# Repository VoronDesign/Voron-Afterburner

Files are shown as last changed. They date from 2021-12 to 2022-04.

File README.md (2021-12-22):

# Voron Afterburner Upgrade

Image of Voron Afterburner

## VORON Afterburner Upgrade

Voron Logo

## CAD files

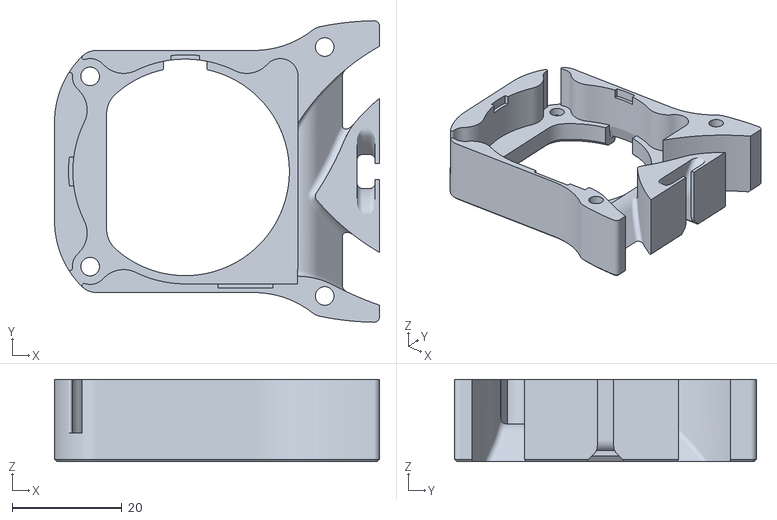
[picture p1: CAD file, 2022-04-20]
STLs/blower_housing_rear.stl
59.3 x 55.0 x 15.0

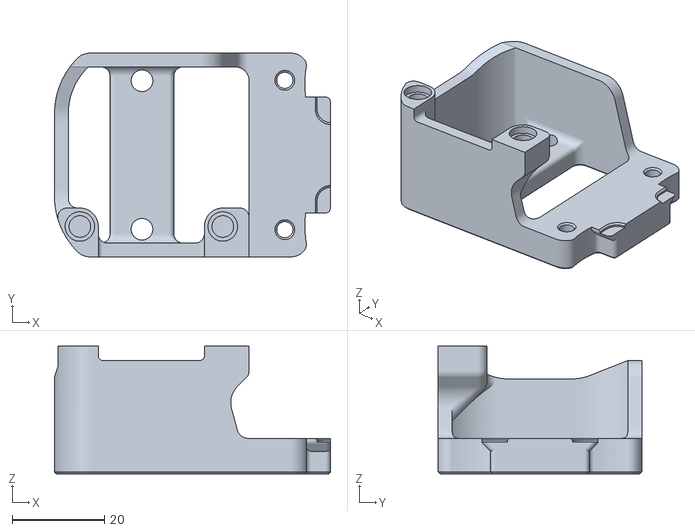
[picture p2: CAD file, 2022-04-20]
STLs/Bowden/bowden_rear.stl
59.9 x 44.2 x 27.7

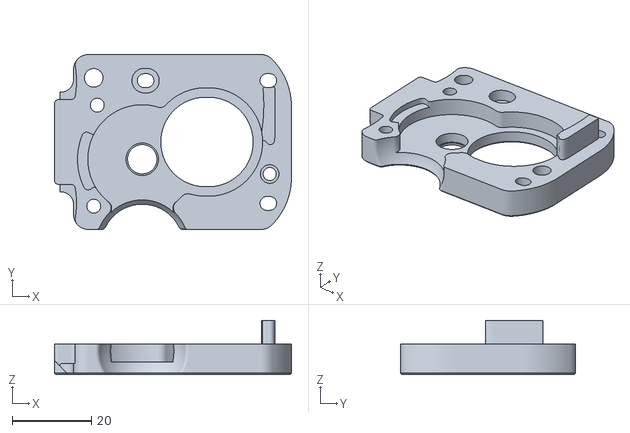
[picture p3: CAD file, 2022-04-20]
STLs/Direct_Feed/extruder_motor_plate.stl
59.9 x 44.2 x 13.7

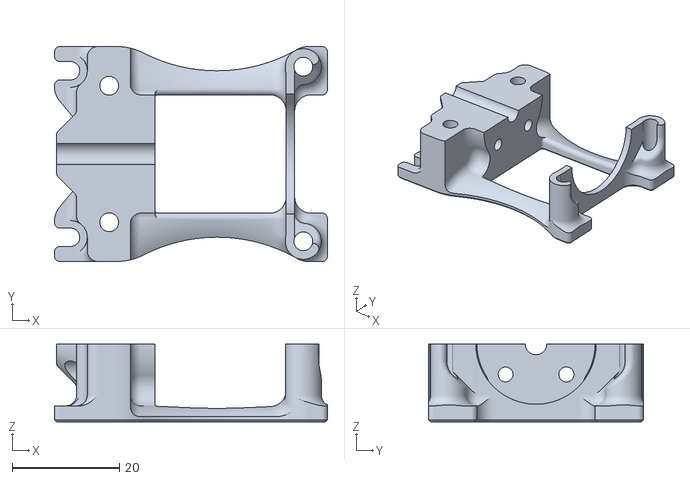
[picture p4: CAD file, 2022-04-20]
STLs/Printheads/Dragon/printhead_rear_dragon.stl
50.8 x 40.0 x 14.5

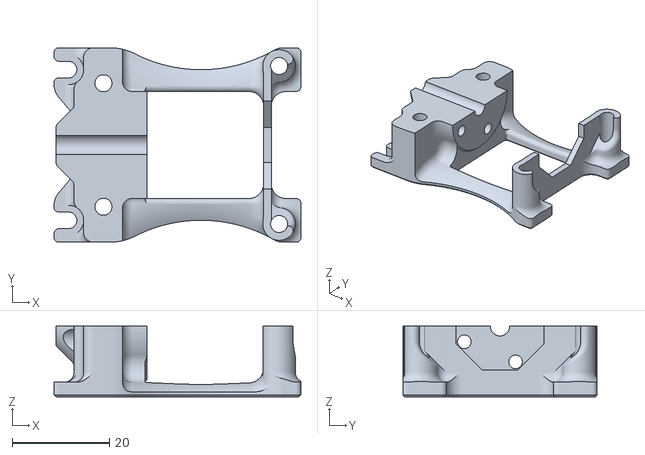
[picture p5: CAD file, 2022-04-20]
STLs/Printheads/Dragonfly_BMO/printhead_rear_dragonfly_bmo.stl
50.8 x 40.0 x 14.5

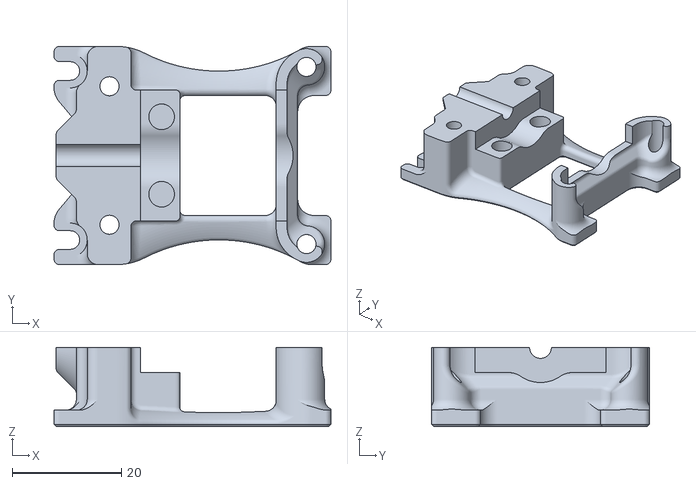
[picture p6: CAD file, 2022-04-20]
STLs/Printheads/Dragonfly_BMS/printhead_rear_dragonfly_bms.stl
50.8 x 40.0 x 14.5

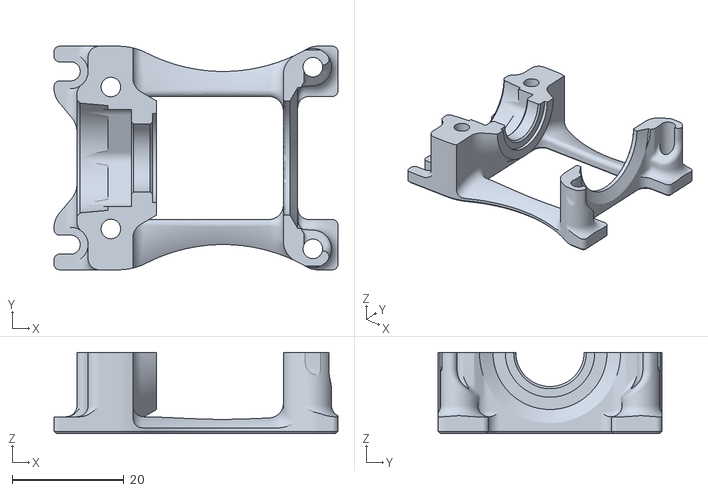
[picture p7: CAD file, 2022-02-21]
STLs/Printheads/E3D_Revo_Micro/printhead_rear_e3d_revo_micro.stl
50.8 x 40.0 x 14.5

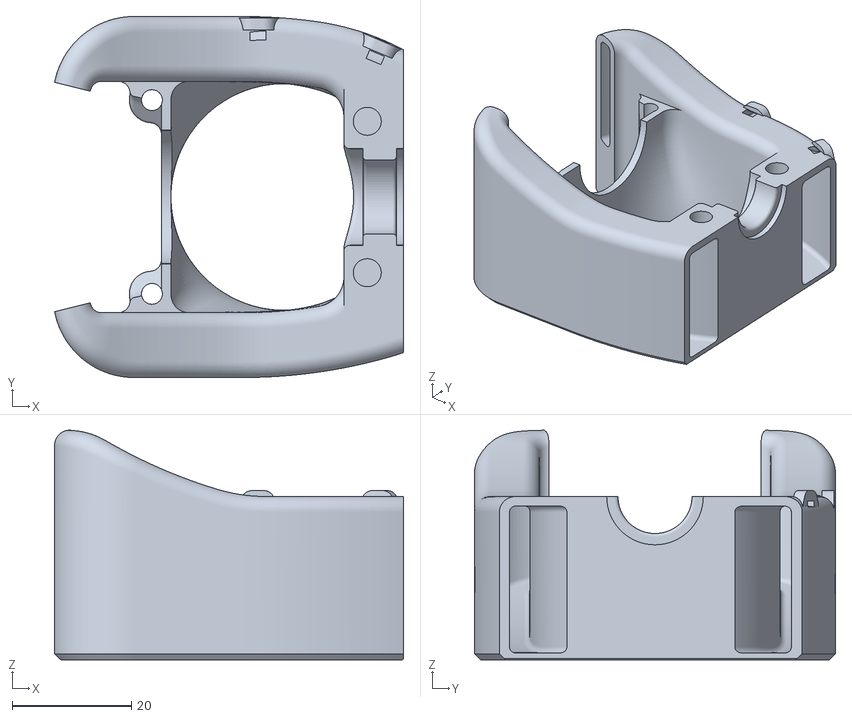
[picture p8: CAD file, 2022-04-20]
STLs/Printheads/E3D_V6/printhead_front_e3dv6.stl
58.6 x 60.6 x 38.5

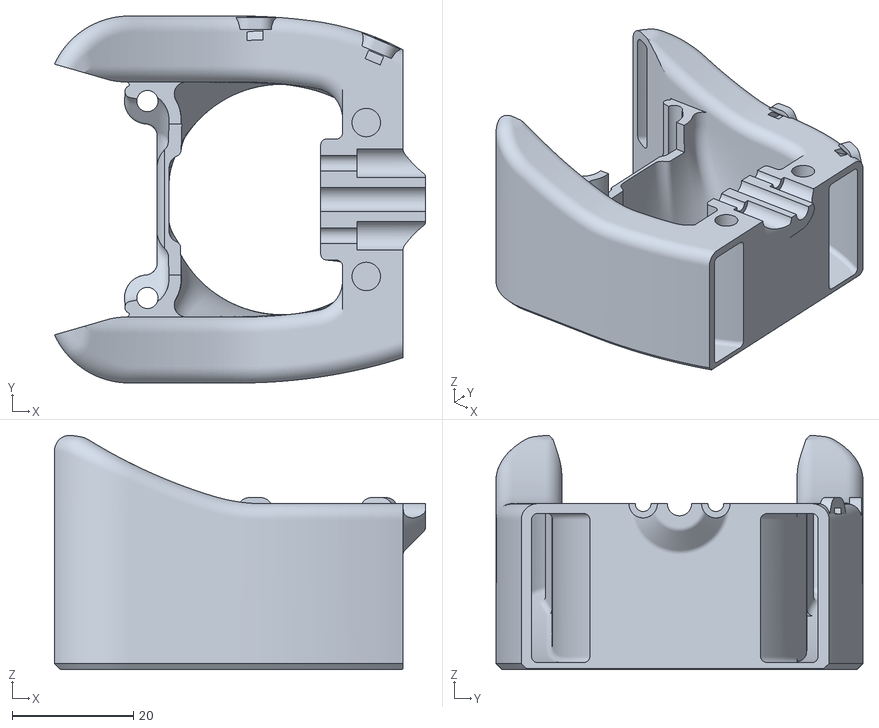
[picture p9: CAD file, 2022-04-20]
STLs/Printheads/Slice_Mosquito/printhead_front_mosquito.stl
61.2 x 60.6 x 38.7

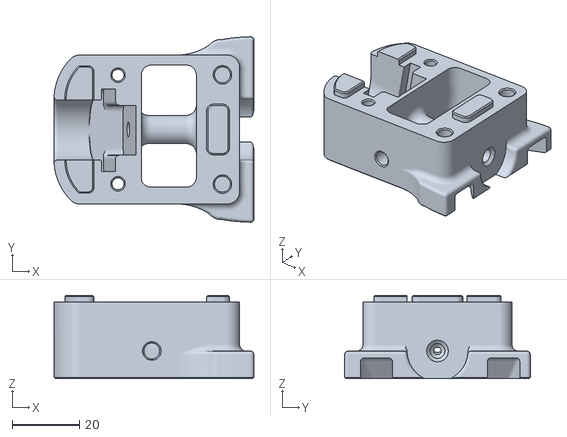
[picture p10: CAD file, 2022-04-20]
STLs/Bowden/bowden_single_front.stl
59.3 x 55.0 x 24.7

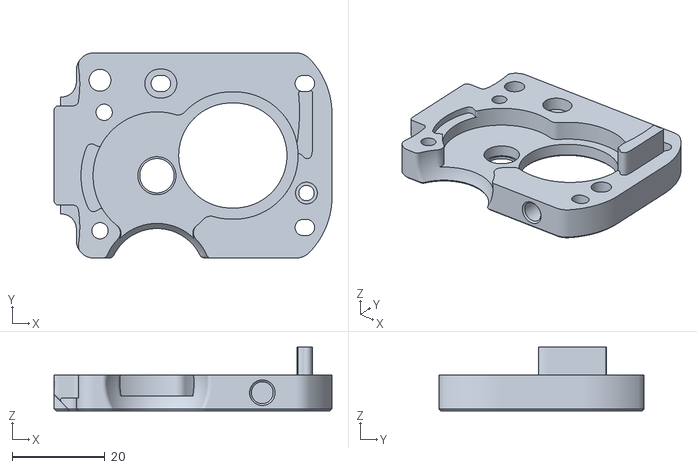
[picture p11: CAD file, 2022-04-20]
STLs/Direct_Feed/extruder_motor_plate_for_pcb.stl
59.9 x 44.2 x 13.7

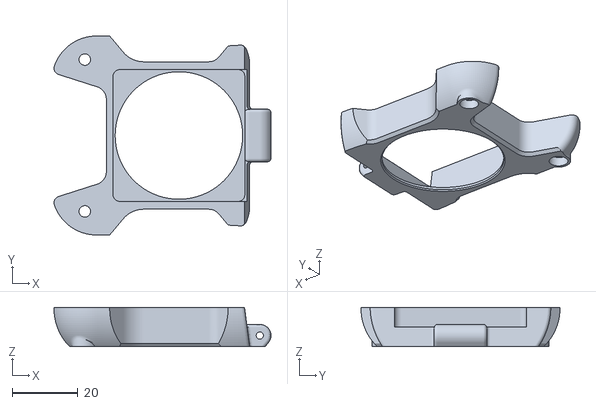
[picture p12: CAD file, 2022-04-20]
STLs/hotend_fan_mount.stl
66.1 x 60.6 x 12.0

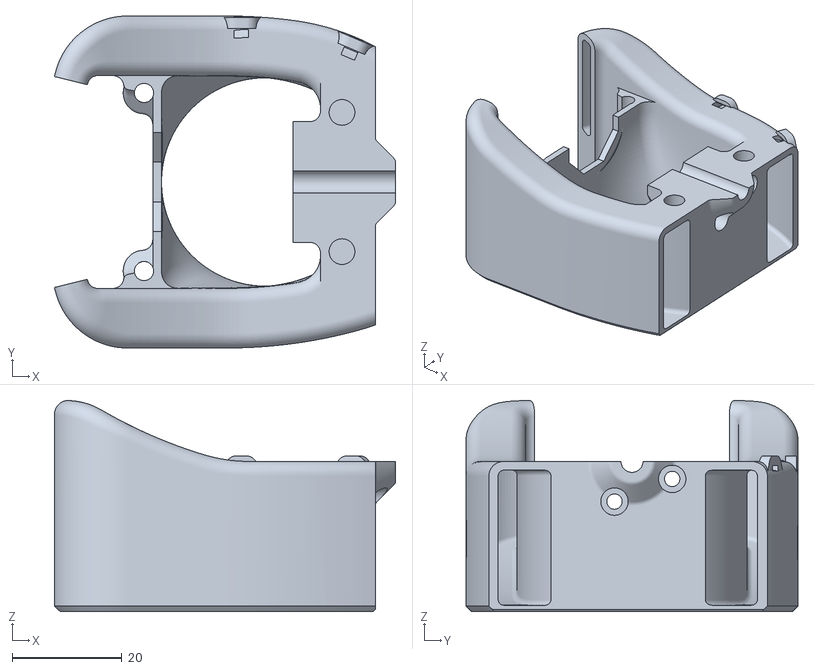
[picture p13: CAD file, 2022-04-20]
STLs/Printheads/Dragonfly_BMO/printhead_front_dragonfly_bmo.stl
62.3 x 60.6 x 38.5

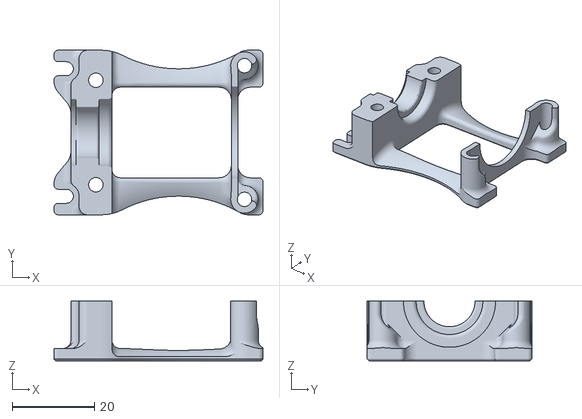
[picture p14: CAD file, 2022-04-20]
STLs/Printheads/E3D_V6/printhead_rear_e3dv6.stl
50.8 x 40.0 x 14.5

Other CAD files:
STLs/Printheads/E3D_Revo_Voron/printhead_rear_revovoron.stl
STLs/Printheads/Slice_Mosquito/printhead_rear_mosquito.stl
STLs/[a]_blower_housing_front.stl
STLs/Bowden/bowden_dual_front_a.stl
STLs/Bowden/bowden_dual_front_b.stl
STLs/Bowden/bowden_single_tl_collet_adapter.stl
STLs/Direct_Feed/[a]_connector_cover.stl
STLs/Direct_Feed/[a]_connector_cover_18.stl
STLs/Direct_Feed/[a]_guidler.stl
STLs/Direct_Feed/[a]_latch.stl
STLs/Direct_Feed/[a]_latch_shuttle.stl
STLs/Direct_Feed/chain_anchor_2hole.stl
STLs/Direct_Feed/chain_anchor_3hole.stl
STLs/Direct_Feed/chain_anchor_SW_2hole.stl
STLs/Direct_Feed/chain_anchor_SW_3hole.stl
STLs/Direct_Feed/extruder_body.stl

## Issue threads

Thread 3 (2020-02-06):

More room for 30 mm rods in XX joints

Kruppes, 2020-02-06:
With a 30,0 mm rod being perfectly flush with the bottom bearing it sticks out of the top bearing ~1mm. This makes the rod touch the printed part and block the rotation once fully assembled. Since the pulley is glued into place it can not be corrected easily after assembly and finding out.

 Can you reduce a little more material above to give room for non perfect alignment or add the ideal position of the pulley (in mm length of the rod sticking out on each side).

FHeilmann, 2020-10-15:
Since Afterburner has since left the beta stage (I assume this issue pertains to the beta release) I'm going to close this issue, if the issue is still present on the release version, feel free to reopen it!

-Florian

Closed 2020-10-15.

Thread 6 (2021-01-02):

Inconsistent extrusion / Z Banding

Roycinger, 2021-01-02:
Hi,
first and foremost I would like to bring this issue to attention where we can track it all together properly. Discord doesn't seem the right place for me as messages and focused discussions get overscrolled and interrupted with non-related topics very quickly.
Before I start I want to mention that I don't expect this issue to get solved by the Voron Team alone. Moreover, I want to evaluate this together with you so that the entire Voron community can benefit from it.

I started facing this extrusion issue when I completed my 100%-built-by-specc Switchwire. In the beginning I was thinking that the printer wasn't properly tuned yet. So I went through all the tuning steps (aligning belts, rails, tuning for filament, E-steps, run_current etc). The result didn't improve within about 90 or more test prints (where I tested every single extrusion related slicer and firmware setting).
Over the course of a few weeks, I partly reassembled the SW again, paying special attention for accuracy, squareness, etc, results didn't improve. At this point I was still under the impression that the issue was on my side as the issue still persists.
To rule out the AB, I converted my SW to bowden and the issue was gone! So I came to the conclusion that there might be a problem with the AB itself.
Because of that, I reprinted the Clockwork parts, changed the TL gears, changed all bearings, changed the motor, changed the entire hotend, precisely cut the PTFE tube. No change in results at all.
For informational purposes, this is my config: https://pastebin.com/nyULd4ca
Fast forward:
Up to yesterday, I noticed that more and more people are facing the same or similar issues, even if they might be fine with the results.
I got sent a plethora of pictures which I was allowed to use in this Git issue. They all more or less show the same problem,
Please note that most pictures where shot with "bad" light, directly from the top to make the issue apparent.
These are kinda mixed from specc-built v2.4's and SW's.
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
Cubes from my SW:
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
Random v0 part printed with my SW:
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
Another set of v0 parts:
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

For my part, I could rule out any looseness in the kinematics or topics related to filament (as I made tests with PETG, PLA and ABS from various brands).
Those defects appear either random (not at fixed heights) or depending on print features within the model (plateaus, holes, etc).

For me it comes down to a few points:
- requirement of quality is not the same for every user (they might live with the defects)
- There might be issues with either the AB internat geometry or the ABS shrinkage bothering with the tolerances
- related to the point above: A genuine Bondtech BMG in a direct drive situation in another (non Voron) printer works perfectly without showing these defects
- Using a bowden extruder (M4 in this case) eliminated the issue

Yesterday, I had a brief conversation with Ray. I introduced the topic "Prusa Issue 602", which looks awefully similar to this.
I would be happy if you could either assist with this issue or shed some light on it.

Thanks in advance!

toskium, 2021-01-02:
Thank you for submitting this issue. I do experience the same results and I was not yet able to pin down the root cause of it.

toskium, 2021-01-02:
To add something to the issue. I was doing input shaper calibration and the outcome of the calibration print is imho interesting.

Since klipper calculates the extruder acceleration according to the xy acceleration the striping pattern changed accordingly.

See the attached picture.
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

It appears more or less intense starting from acceleration 1250 all the way up to 7500.

BladeScraper-Designs, 2021-01-02:
Same here as well.  tried new BMG parts, various flow settings, various accels and speeds from 30mm/s and 500acc to 120mm/s and 5k accel, etc.

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

Gizzzle, 2021-01-02:
Can confirm the issue.
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

mgrl, 2021-01-02:
Just built a v1.8 with bowden. I think I don't see the effect, which aligns to your proposal, right?

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

toskium, 2021-01-02:
> Just built a v1.8 with bowden. I think I don't see the effect, which aligns to your proposal, right?

Yes, correct. The issue seems to be exclusive to the clockwork extruder. Your input is much appreciated!

Serpreme, 2021-01-03:
Can we make a list of the items that are used and not used between the bowden and direct drive? The gears, motors, wiring, and then we can slowly eliminate those items. We can try to test for things like EMI for example

Gizzzle, 2021-01-03:
> Can we make a list of the items that are used and not used between the bowden and direct drive? The gears, motors, wiring, and then we can slowly eliminate those items. We can try to test for things like EMI for example

I can eliminate every part on the Afterburner except the hotend, but that's not the problem since the other guys are using a dragon while I'm using a v6. Also EMI is not the issue since I used another motor without cable management which lead to the cable not crossing another cable in it's way to the board.
Stepper driver was also swapped from a LV8729 to a TMC2209

BladeScraper-Designs, 2021-01-03:
Added details to my post.

jdlongenecker, 2021-01-03:
Hello everyone, I have a recommendation to make.

In order make a proper comparison, I recommend that someone mount a BMG extruder directly to Afterburner in place of the Clockwork module. If the issue clears up, then you can root cause the issue to be something with the clockwork module itself. If the issue persists, then the source of the issue is something else.

I would not compare a bowden and direct drive mount of the same extruder--the physics of printing through a long tube with springy filament is different than when the extruder is right on top of the hotend.

Gizzzle, 2021-01-03:
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

We had the idea too, but that's nearly impossible because of the small footprint of the afterburner.

JayAwesome87, 2021-01-03:
Same problem since day one. I'm using a Galileo Clockwork now and the problem still persists.

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

Roycinger, 2021-01-03:
> In order make a proper comparison, I recommend that someone mount a BMG extruder directly to Afterburner in place of the Clockwork module. If the issue clears up, then you can root cause the issue to be something with the clockwork module itself. If the issue persists, then the source of the issue is something else.

This is easier said than done because of a few points:
- The BMG is 2.6mm thicker than the Clockwork:
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
- The filament path is not the same as the Clockwork's:
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

All in all, almost every single part of the AB would have to be redrawn to accomodate a BMG

jdlongenecker, 2021-01-03:
> Same problem since day one. I'm using a Galileo Clockwork now and the problem still persists.
>
> 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

Is this the version with planetary gears? If so, this would imply that it's not the Clockwork module itself but something else :)

Gizzzle, 2021-01-03:
I'm using my Ender Switchwire Conversion

jdlongenecker, 2021-01-03:
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

Let me see what I can do, I would like to support your testing! I do not have time right now for diagnosing the issue but I may be able to provide some parts you can print with to test the theory.

JayAwesome87, 2021-01-03:
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

Yep, the one with planetary gears. Printed on a Voron 2.4 250.

jdlongenecker, 2021-01-03:
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

I am thinking something simple like this--no part cooling, but it should still show improvement
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
9ary, 2021-01-12:
If you mean the idler, it's indeed supposed to self align when the filament is in. That's how it is in a stock BMG body too.

hhammarstrand, 2021-01-12:
> If you mean the idler, it's indeed supposed to self align when the filament is in. That's how it is in a stock BMG body too.

I was referring to the shaft assembly. The idler didn't have nearly as much play as the shaft assembly
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

9ary, 2021-01-12:
Alright, this might be worth looking into then, because it really needs to be constrained properly.

ctilley83, 2021-01-23:
Seems my afterburner is not affected.  You didn’t cut your ptfe tube too long did you? There was an issue on the prusa forums that if the ptfe tube gets compressed during assembly, it can lead to similar extrusion issues. The particular issue was with a prusa mini which has a similar geared setup to the afterburner. Seems that after properly trimming the ptfe tube, the issue disappeared.

ctilley83, 2021-01-23:
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

that’s the worst downlighting I could get.  Extrusion seems pretty spot on.  Only a few inconsistent spots around features

rcfishhunt, 2021-01-23:
I am not really sure.  I had to guess my length.   For the ptfe

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

JustinCaseOfWolf, 2021-01-23:
> I am not really sure. I had to guess my length. For the ptfe

i have cut the afterbuner top in half so i can measure exactly the ptfe length. not quite the fastest / cheapest way to do it but i know for sure it is the correct lenght. so in my case that does not apply

JustinCaseOfWolf, 2021-01-23:
@ctilley83 different colours shows different surface. while yours is less obvious than the black above i am sure with the right light your can be made more visible.

rcfishhunt, 2021-01-26:
I am making some progress with this.  And it might seem simple.   The build instructions say nothing about using the nylon washer on the thumb screw from the bmg parts.  I took mine off and replaced it with a thin flat washer to keep the spring from digging in to my printed parts and was able to reduce spring tension and it is making an amazing difference.   Still loosening to get the best results.   But her is with and without the nylon spacer
![Uploading 20210126_174702.jpg…]()

Gizzzle, 2021-01-27:
> I am making some progress with this. And it might seem simple. The build instructions say nothing about using the nylon washer on the thumb screw from the bmg parts. I took mine off and replaced it with a thin flat washer to keep the spring from digging in to my printed parts and was able to reduce spring tension and it is making an amazing difference. Still loosening to get the best results. But her is with and without the nylon spacer
> Uploading 20210126_174702.jpg…

Unfortunately I can't see your pictures, but I have used the washer from the beginning and my print quality was bad. So maybe it's only a coincidence in your case.

rcfishhunt, 2021-01-27:
Ok I will try to reload them

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

ehellman, 2021-02-04:
I have followed this discussion for a while and sadly haven't been able to chip in because I am still waiting for my POWGE package which contains all my pulleys etc.

Have printed the entire AB though, inspected, measured, tried V6 and Dragon variants. While I do have some ideas, first I would like a question answered, if anyone has time:

We see a bunch of calibration cubes here, great. But could someone take the time to create a vase mode print and post it here? Doesn't have to be a super advanced vase. I usually print a 100x30x120 (x, y, z) rectangle in vase mode to make some basic tests. Then I switch over to one of the widely available vase models, but the simplest ones are the ones that could show you the biggest effects. It should have some shapes, but not go overboard with it. Would be an interesting test at least.

mateuszbrzezinski, 2021-02-05:
I'm experiencing same issue, V2.4 with AB-BN-25 cooling
But how bad it looks it depends at what angle you look at and if the light is harsh or not.

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

mateuszbrzezinski, 2021-02-05:
What if that is some bug in Klipper? SKR? TMC2209?
Anyone using Duet to compare this?

9ary, 2021-02-05:
I've rebuilt my extruder with my new motor, and I'm not affected apparently. I'm using Klipper on a Duet 2 WiFi (TMC2660), nothing is tuned yet.

mateuszbrzezinski, 2021-02-06:
I was printing test cilinders, so there is no any sharp angles, so to exclude such variable. Then that is interesting, when nozzle crosses Y center axis of model, so before crossing this one of the AB drivers is rotating faster, then after crossing the other motor is rotating
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

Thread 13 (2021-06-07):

blower_housing_rear wire clearance

geoffrey-young, 2021-06-07:
blower_housing_rear doesn't quite have enough clearance for the wires of the BOM (2.4) blower, leaving two options - wires are crushed against the housing, or remove the wires from their clips and risk them coming detached from their solder points.  Both happened to me.

I made a very minor adjustment to the housing that alleviates the issue, which I thought would be good to illustrate

[marked up (master) stl showing location of required fix](https://www.dropbox.com/s/xla9d09jeyvuyxh/blower%20housing%20fix.png?dl=0)
[printed part with fix](https://www.dropbox.com/s/xcgux1s7hpevfm0/blower%20housing%20issue.jpg?dl=0)

Fix available in https://github.com/VoronDesign/Voron-Afterburner/pull/12

stvptrsn, 2021-08-31:
A fix for this was intended to be included in the May update.  I'm not sure why it didn't make it in but I just included it along with several other corrections.  Thanks for pointing it out.

Closed 2021-08-31.

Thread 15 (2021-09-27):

Afterburner heatset holes are 4.8mm instead of the 4.7mm used everywhere else.

ChaosBlades, 2021-09-27:
After building a v0 and working on a Switchwire mod I have noticed after printing the Afterburner parts a lot of the heatset holes are 4.8 mm instead of the standard 4.7 mm used everywhere else. This causes the heat sets to just fall into the hole and not actually melt any plastic. This seems to be a problem with all CAD for other printers that use the Afterburner as well. It is probably an issue with the STLs as well.

netweaver1970, 2021-09-27:
I did see in my MJF printed version of the afterburner AB-BN30 part cooling fan duct, that my heatsets were easily melting in, seemingly ok but had very little pull-out strenght. I blamed it on the MJF, as that was a fraction of percent bigger than an ABS part. But if it's indeed true about the slightly bigger holes, then I'm not surprised at all...

ChaosBlades, 2021-09-27:
Almost forgot. The ascent colored part cooling fan duct self tapping holes are also 0.1 mm larger than they are supposed to be as well. My screw just fell right in and didn't cut any thread. With that said I don't see why these are not heat sets as well. I modified my CAD of the Afterburner to put heatsets here.

0x3333, 2021-12-24:
This issue has been considered for the stealth burner release?

AaronHerrick, 2022-01-08:
> This issue has been considered for the stealth burner release?
Ihave checked SB, the only heat inset holes I have seen off spec in SB are on the probe bracket (4.8mm) and toolhead (4.6mm).  I think it is likely the ones on the toolhead were tightened by design.

qema36, 2022-02-08:
This seems to be an issue with the SB, I just printed a SB and the holes in the CW2 and SB are too big for the heatset inserts to grip into.  They don't quite fall into the hole but once pushed in they can turn in the plastic with a bit of force.   Same profile was used on a SW and I had no issues with the hole size.

Closed 2022-04-21.

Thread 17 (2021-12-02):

Receiving holes on printhead_rear_mosquito too large

soapyshazbot, 2021-12-02:
Non heat set holes on this piece are too big for M3 bolts so the bolts do not cut a thread when inserting.

soapyshazbot, 2021-12-03:
Confirmed holes are 3.5mm diameter.

bdbell, 2021-12-03:
That is as intended.  The M3x40 passes through the printhead_rear part and threads into the headset inserts in the carriage.

Closed 2021-12-03.

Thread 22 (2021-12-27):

Holes in [a]_stealthburner_main_body_beta0.stl

elcrni, 2021-12-27:
Hotend cooling fan bay has 3 corners rounded and one left without fillet, this results in slicer having issues and the print has a hole in the wall. as seen on attached images
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
.

tnap1979, 2021-12-27:
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
Seems to be more of a cosmetic concern and less of a leak or performance issue.. but it's there none the less

FHeilmann, 2021-12-27:
Which slicer are you using? What's your "detect thin walls" setting?
Here's my slicing result with PrusaSlicer 2.4.0 and "Detect thin walls" enabled:

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

elcrni, 2021-12-27:
Also using Prusa 2.4, mz settings as attached
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

FHeilmann, 2021-12-27:
what are your extrusion widths?

elcrni, 2021-12-27:
All my extrusions are forced to 0.4mm

wile-e1, 2021-12-27:
This issue has been corrected with the update of [a]_stealthburner_main_body_beta1.stl

The missing fillet was added and material was also added to the front facets to help increase the wall thickness on this layer.

raymondh2, 2021-12-28:
Issue fixed in #21 Will leave open for three days before closing to confirm fix.

elcrni, 2021-12-28:
Is there a file [a]_stealthburner_main_body_beta1.stl available to download somewhere to test? many thanks

raymondh2, 2021-12-28:
https://github.com/VoronDesign/Voron-Afterburner/blob/sb-beta/STLs/Stealthburner/a_stealthburner_main_body_beta1.stl

Closed 2021-12-28.

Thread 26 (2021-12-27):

Phaetus BMS part cooling ducts are too high

DorjeDorf, 2021-12-27:
I just finished mounting a Phaetus BMS onto the SB.
I noticed the ducts are high enough that they blow onto the heatblock - especially if a sock is present. This is very visible also during PID tuning.

Photos attached.
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

wile-e1, 2021-12-29:
Can you please measure from the top of the toolhead to the tip of the nozzle?

I check the CAD and everything matches what it should be.  I did, however, find an issue with the CAD provided by Phaetus that showed the radius of the heatsink being 3mm but in reality it is more like 1.5-2mm so I have a feeling that your hotend may not be seated fully.

plumpcheek, 2021-12-29:
Mine Phaetus BMS with beta0 toolhead and I measured from the tip of nozzle to the top toolhead (w/o ptfe collar) is 48.93 mm.
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
.

DorjeDorf, 2021-12-29:
In my case it's 51mm.

When you say hotend not being seated fully - do you mean the heatbreak in the heatsink or rather the whole thing inside of the printed part? If it's the latter - below is a picture to show the fitment.

The one thing that has me curious is also visible on the photo from @plumpcheek - should a part of the heatsink be sticking out like that? My BMS is black and it's a touch more tricky to capture on a photo, but I see the same thing.

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

plumpcheek, 2021-12-29:
Well, look like Phaetus strike again, my BMS is well within the back bracket, and you can count the number of heatsink fin, mine is 6 and ur are 7 :) This BMS purchased fom Trianglab as a drop in replacement for Ender 3 v2 hotend (that what Phaetus advertise), turn out it's not since its too short for origin E3v2 hotend fan duct, back then I remember I had to print a new duct for it, my wild guess is they extend the length to become a real drop in replacement hence yours is longer.
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

plumpcheek, 2021-12-30:
And may I ask what version of your back bracket, look like the corner radius is corrected with your hotend, if you used beta0 version, so there two types of BMS hotend: one is short and narrow corner and one is long and wider corner :)

DorjeDorf, 2021-12-30:
I used the Beta0 for CW2 one.

mathisschmieder, 2021-12-31:
I can confirm the 51mm length of a recently bought Dragonfly BMS. Well, more like 50.93mm

DorjeDorf, 2021-12-31:
Here are my measurements just to keep it in one place.
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

DorjeDorf, 2022-01-01:
I just printed out the Beta1 toohead.

Things I noticed for the BMS.

1. The name of the toolhead on the Front part - now reads BMO and not BMS.
2. In my case, the change to the corners for mounting don't change anything, but are a nice touch :)
3. **No changes** in terms of the cooling ducts. Their bottom tip starts at the end of the heatblock when it's without a sock. When I put a sock on - it's clearly vislble that the air will blow on the heatblock and not on the nozzle. I did a water bowl test - there was center point for air converging beneath the nozzle. It got a bit better when I took the sock off, but still, nothing like what I can get with the Dragon SB toolhead.

AaronHerrick, 2022-01-05:
there are 2 different phaetus BMS toolheads. the older one, with 6 fins, is the one we did the mount for. the newer one, that they changed without telling anyone, has 7 fins and its slightly longer.  I'm hoping its about the same size as the Zodiac BMS, plus or minus .25mm that should be close enough

mathisschmieder, 2022-01-05:
According to these https://cdn-3d.niceshops.com/upload/file/Technical_data_sheet_for_BMS_Hotend[0].pdf specs, the Zodiac BMS is 45.36mm from top of heat sink to bottom of heater block. This is absolutely in line with my recently bought 7-finned Phaetus Dragonfly BMS and with what DorjeDorf posted.

mathisschmieder, 2022-01-06:
As far as I can tell, the beta2 parts fix this issue, at least with the 7 fin version. Top of toolhead to nozzle tip is bang on 61.5mm

raymondh2, 2022-01-07:
@DorjeDorf Does beta2 fix these issues for you?

DorjeDorf, 2022-01-11:
Bah I missed the callout. I will print it tomorrow and let you know.

DorjeDorf, 2022-01-13:
Can confirm. Looks good. Haven't printed yet, but water bowl test went through great. Thank you.

Closed 2022-01-11.

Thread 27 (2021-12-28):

StealthBurner / ClockWork2 odds and ends...

Durahl, 2021-12-28:
So, I've now assembled my SB/CW2 Combo but I've yet to test it on my Voron 2.4 due to me still working on HartK1213 Toolhead PCB and an ERCF Toolhead Sensor compatibility - While the latter wasn't _that_ much of a problem the former still is - Kinda wish the Cable Door would offer like two more mm of free space inside:
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
I'll most likely have to modify the PCB by turning the PCF Board Connector into a Pigtail one 😑

**Aaanyway... A bunch of other things I've noticed along the ride that may also be of interest for the general public:**
1. **Manual Page 15** - The supposed M3x20mm screw should most likely be an M3x25mm too
( akin to the three other M3x25mm ones that hold the two CW2 halves together via Heat Inserts ).
2. **Part Interference** - The marked corners could use some trimming as they're interfering with the Idler BMG Teeth:
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
3. **Part Printability** - Continuing the split along the red marked line would significantly improve printability of the Cable Door as the small triangle ends up being a R.P.I.T.A. to print without it turning into a hot mess:
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

wile-e1, 2021-12-29:
> 1. **Manual Page 15** - The supposed M3x20mm screw should most likely be an M3x25mm too
>    ( akin to the three other M3x25mm ones that hold the two CW2 halves together via Heat Inserts ).

I put in a change request for the manual 2 days ago, so it should be updated soon.

> 2. **Part Interference** - The marked corners could use some trimming as they're interfering with the Idler BMG Teeth:

This has been addressed in my latest PR.
[https://github.com/VoronDesign/Voron-Afterburner/pull/38](url)

> 3. **Part Printability** - Continuing the split along the red marked line would significantly improve printability of the Cable Door as the small triangle ends up being a R.P.I.T.A. to print without it turning into a hot mess:

Unfortunately, this lower corner needs to be the way it is in order to make it easy to slot the hotend wires in.
If this portion is turning into a hot mess, Maybe try lowering your printing temp, increasing cooling, or increasing your threshold for layer speed reduction based on layer time.

raymondh2, 2021-12-30:
Will close once verified

Closed 2022-01-21.

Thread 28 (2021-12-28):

More difficult to print than existing Voron parts

zapta, 2021-12-28:
Never had a problem printing Voron parts with my v2.4 but this one gave me unexplained artifacts. Lamination is good and the part is strong but there are very visible artifact lines that reflect features on the inside of the part. This is not a layer shift since that layer is OK on the rest of the perimeter of the part.

I don't know if it's just me would would be useful to stay within the current requirements of Voron part printing.
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

evandepol, 2021-12-28:
@zapta i wonder if these are likely slicer-profile-induced artifacts. At first glance it seems you might have too high of a flow rate, since outside walls appear to be "bulging" differently when outside walls are thin (towards the bottom of the picture) versus thicker/more room for the filament to go.

zapta, 2021-12-28:
Erik, I am printing with Super Slicer, esteps calibrated and 0.95 flow. I
will try to recalibrate my printer and print again and will report here.

My point is that there is a potential that this model is more demanding
from existing Voron parts so it will be interesting to see if you will get
similar reports from others.

On Mon, Dec 27, 2021 at 6:29 PM Erik van de Pol ***@***.***>
wrote:

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

bartoszwas, 2021-12-28:
It's white it means that is layer separation due to shrinking.

Scroeder, 2021-12-28:
I have the same 2 lines. Interesting.

wile-e1, 2021-12-28:
While I admit that the SB main body is challenging to print, it **can** be printed without seeing these artifacts.  You're seeing these issues in these locations because of the change of cross-section there.

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

Do you have a chamber thermistor?   (if so, what temp is it reading?)
What material is this with?

Scroeder, 2021-12-28:
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

I print with Esun Abs+ with around 40°C in chamber.   Imho print quality is perfect on other parts.

zapta, 2021-12-28:
The lines look white because of a lighting artifact, they are not white in
reality or when the light is from a different direction.

I was printing with Hatchbox black ABS, chamber temperature rises up to
45C. The print with the lines was done with no pre-heat soaking time, just
as I have done with all other Voron prints and never had a problem. I am
trying now with a 1h soaking time, to let things stabilize better, will
report the results here.

The part may be printable but if it raises the bar for Voron parts
prinability, that decision should be made consciously.  The problem is not
structural but aesthetic, at one of the most visible parts of the design.

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

zapta, 2021-12-29:
Here is the print with the 1h soaking. Overall its good but still a
deformation at the top of the part (as installed in the printer). The
profile should be made of two slopes but one if them is printed
concave (see annotations in pictures below).

[image: 2021-12-28_16-05-46.jpg]

[image: IMG-3212.jpg]

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

Scroeder, 2021-12-29:
I have found a picture on Facebook with the same strange lines.
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

jarrettv, 2021-12-29:
My print had these lines too but I assumed it was more an adhesion issue. I think the surface area in this area is just smaller overall than AB/ABBN and makes it more likely for the part to pull away from the bed near the top. A small loss of adhesion in that area results in lines in the print. I'm using SuperSlicer too fwiw.

zapta, 2021-12-29:
After another examination, I believe that the problems in my print are due
to adhesion issues at the top end (as installed in a printer) of the part.

1. Examining the front face with a ruler shows that the top end was lifted.

2. If cut the model in the slicer and print only the top end, it comes
clean.

The structure of this part, long and minimal first layer area on one end
makes it more difficult to print than normal Voron parts. CW1 solved it by
splitting the face into two parts.

On Wed, Dec 29, 2021 at 10:12 AM Jarrett Vance ***@***.***>
wrote:

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

bartoszwas, 2021-12-29:
That's the problem. When adhesion is good there's risk it will crack like on zapta's picture (white lines). I printed it three times with ASA filament which I never had any adhesion issues (I've printed all Voron 2 parts that filament) and every time top part was lifted.

khay8485, 2021-12-29:
I had the same Issue with warping of the 5015-End of this part, which resultet in those thickened lines on the part. For me, changing filament did the trick. Changed from Fiberlogy ABS to eSun ABS+ to make it work. Surface was cleaned properly.

zapta, 2021-12-29:
This is a question to the designers of the new extruder.

Is it a goal for you that everybody that can print other Voron parts can
also print this one or is it OK to have additional
materials/printers/processes/skills requirements in order to print this
part successfully?

My preference is to prioritize printability and voron accessibility over
form.

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

SellA, 2021-12-30:
I think that these parts are more challenging than standard voron parts, but nothing compared to non-optimized parts. I would look from another perspective: if you are printing with a Voron, are you sure you are getting good enough prints from your printer? I've printed it in ABS and some tests in PLA and yes, i have some artifacts and small aesthetics issue, but i get those on all my prints and i'm still investigating it. Also my PIF parts that comes from 2 different machines (both from Stephan) got 2 different look: some are perfect and some shows layers bands.
So if this works as good as ABBN and got all that new features packed on a single toolhead, i think we must try to increase our printers quality and reliability. Maybe it's not easy but it will pay off on all other prints that we do.
Obviously if the part can be optimized i hope it will be done by developers.

zapta, 2021-12-30:
I reprinted the part with purple Elmer glue, bed adhesion adhesion was very good and the problem disappeared though the face is a little rough because of the glue, even after washing it out. This confirms that the cause is bed adhesion.

Increasing the first layer surface will make this part more printable without scarifying functionality, e.g. by increasing the width from 3mm to 7mm in the picture below.

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

elcrni, 2021-12-30:
my prints dont have any lines, as clean as it can be. turn on 'detect thin walls' as the lines are most likely due to lines overlapping.

hackerjack42, 2021-12-31:
I see the same line on my latest ASA print.  Textured plate....clean.....Prusament ASA....."beta 2" main body.  Beautiful print other than the line.  I checked the face for flatness with a straightedge and it did indeed lift at the top of the part cooling fan intake.  The contact patch is only about 3mm wide, which in my opinion is too small for an object that is intended to be printed in a filament that is known to shrink.  I'm sure that printing with a brim would resolve this, but it would be better to be addressed in the model itself.  Can that top contact patch be enlarged without compromising the design aesthetics?

to-the-nth, 2022-01-01:
I agree these parts are harder print.  I've printed 3 sets of Voron 2.4 parts in eSun and Paramount ABS with a 51-55C chamber (Elmer's Xtreme glue stick slurry on FR4 110C bed -way better than Purple). I got occasional lifting on the first set of parts, so now I just print with a brim and have had -0- failed prints.  Brims are a pain to clean up, but post results are excellent in ABS.  No lifting issues printing StealthBurner with a brim.  But a Stealth test print without a brim failed spectacularly. I am not a fan of eSun ABS+.  Colors are off.  ABS+ heat distortion temp is only 73C compared to 78C for ABS, and it does not clean up well if you have to use a brim or otherwise trim.  Prusament ASA looks interesting but limited color selection.  Amazon has Polymaker ASA might be worth looking at. We need to error on the side of being able to do consistent prints for the masses.  Scary when PIF parts have lifting.

I had bridging issues on the left duct in the pic below.  It eventually did complete the bridge, but it left a deposit of spaghetti underneath while trying.  I ran some test prints, but with the 55C chamber, there's not enough cooling and stuff just sags, so on the print below I resorted to using supports in Simplify3D.    Tried painting support in SuperSlicer and disabled no support under bridge, but couldn't get it to work. Wonder if it is getting confused because the base surface is contoured and not flat.

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

Durahl, 2022-01-02:
I may have missed someone mentioning it but [those lines](https://user-images.githubusercontent.com/2184769/147517747-0ea26853-f266-4405-8410-63f3154b649c.png) are caused by the **Top Layers** that are now also being generated at those Z-Layer Heights causing both the Z-Height generation to slow down but also contracting thus resulting in the newly generated layers above those areas to appear where they're supposed to while the previous layer underneath them have noticeably shrunken down.

I started my Voron journey on a Prusa i3 MK3S using **Generic ABS** ( couldn't get the much revered ABS-Plus at the time ) but have since changed over to **Dutch Filament ASA-X** that has solved a lot of my woes I had with the ABS by simply printing balls to the walls fast **_and_** at full fan speed ( not possible on the ABS I used ) which I assume cools the already laid down filament fast enough before it can add up for enough force to curl up on me.

[In this video](https://youtu.be/HPOSy8ITktM) you can see the finished Toolhead in motion under changing light conditions and as a still under harsh light conditions where you can _ever so slightly_ see the same two lines if you know where to look for:
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

You _could_ try printing those areas without a top layers taking up time to mitigate the issue? 🤔

garyt72, 2022-01-04:
I had a similar issue printing the SB on my first attempt.  I "renewed" by PEI sheet by going over it lightly with ScotchBrite, washed thoroughly with with soap and water, then dried and cleaned again with IPA before letting the sheet sit on the heated bed for ~30 minutes to dry completely.  I haven't had an issue with any the 3 SBs (and other items) I've printed since then.

AaronHerrick, 2022-01-08:
Using a new build plate solved my issues as well.

Closed 2022-01-21.

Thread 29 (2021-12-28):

Chain anchor mounting tolerance/suggested improvement

evandepol, 2021-12-28:
When mounting "chain anchor_3hole-beta0.stl" to "motor_plate-beta0.stl", I put the heatset insert in a tad too deep (perhaps 0.5mm or so). This was enough for the m3x20 BHCS screw to not engage with the thread. So it seems the designed bolt length is a tad too short in some cases.

When i used an m3x25 instead, I blew out the back of the part while tightening.

Suggestion to make this more robust/less critical:
- update instructions to use m3x25 instead of m3x20.
- modify the "chain anchor_3hole-beta0.stl" to include an m3 relief opening so that the longer bolt can go in without bottoming out inside the part.

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

evandepol, 2021-12-28:
Per discussion in discord, this has been resolved by user wile.e by changing the bolt relief on the chain mount.

raymondh2, 2021-12-28:
Leaving open for three days before closing

Closed 2021-12-31.

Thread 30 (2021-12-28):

[SB-beta] guidler tight fitment / suggestion to allow for more tolerance

evandepol, 2021-12-28:
It seems the idler gear assembly is really tight when sandwiched between the motor plate and other half of the CW2.

The cw2 bolts are pretty loose right now (finger tight) to avoid binding, and it still seems there is not a lot of play. I sanded down the idler assembly to give it more play and it's better now, but it seems pretty tight in there. Can the two plastic standoffs holes that meet the motor plate be taller (in 0.4 -0.6mm range perhaps?), or can the holes in the motor plate be made slightly less deep, or can the idler assembly be trimmed in order to give the assembly just a little bit more play? I think the assembly would be more forgiving it had a little bit more tolerance and had easier swing.

Perhaps also of note is that i print on textured plate, which may affect thickness tolerances as well (only on the idler assembly though, since the insides of the CW2 sandwich would not be affected by that). The same printer and plate was used to print Voron 0.1 parts, and that went together easily, so i doubt my 2.4 setup is that far off.

I used motor_plate-beta0.stl, main_body-beta0.stl, [a]_guidler_a-beta0.stl, and [a]_guidler_b-beta0.stl

SellA, 2022-01-01:
I also have some struggles with the tolerances on the guidlers. It seems that they are not all the same measure and too tight also for a press-fit. I attach some sectional view of the beta 2 STL. I think that these tolerances should be made parametric to test it out and try to find the perfect fit.
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

wile-e1, 2022-01-08:
The guidler has an adequate amount of clearance built into it in order to function as intended without binding. The guidler needs to have support on both the front and rear faces in order be fully constrained and prevent twisting from the eccentric loading on the idler.  Having a large amount of clearance would make assembly much easier, but could also come at a detriment to the performance of the extruder.

If the guidler is this tight for you, I suspect you may be over-extruding slightly.  The tolerances on CW2 were tightened up quite a lot in order to improve performance.  Also, you may want to see if you have any blobs or overlap bits that may be causing a tight fit-up.

Closed 2022-01-23.

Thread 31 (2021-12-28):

[SB-beta] Phaetus BMS fit issue with toolhead rear

plumpcheek, 2021-12-28:
File print: stealthburner_toolhead_(phaetus_bms)-rear-cw1-beta0 (and front), the upper corner radius seem wider than the hot-end corner radius lead to the upper end of hot-end not sit flush and the bolt misalignment with hole below (a little, I can force it in). See picture below:
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

wile-e1, 2021-12-29:
The CAD provided by Phaetus does not match actual parts.

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

The radius of the model shows 3mm, but measurements from actual heatsink are around 2mm.  The toolhead will be adjusted to suit.

plumpcheek, 2021-12-29:
Thanks, closing this and wait for new toolhead.

wile-e1, 2021-12-29:
Should be posted tomorrow.

Closed 2021-12-29.

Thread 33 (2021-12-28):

Phaetus BMO part cooling ducts are too high

Krieselwind, 2021-12-28:
distance between nozzle and highest point of fanduct is about 3mm.
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

raymondh2, 2021-12-28:
Duplicate of #26

Krieselwind, 2021-12-28:
40.4mm

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

44.9mm
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

11.6mm
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

raymondh2, 2021-12-28:
Can you please check and make sure your screws aren't bottoming out.

AaronHerrick, 2021-12-28:
I can confirm that the BMO I used to test with is the same overall length.  I would guess that either the screws are bottoming out for you, or something else is preventing the hotend from seating fully.

Krieselwind, 2021-12-29:
Screws are tight. My second BMO was still in use and have the same size.

mathisschmieder, 2021-12-29:
I can confirm both the measurements and the issue. While the 8mm M2.5 screws supplied with the hotend in fact do just bottom out on the heat sink, it is seated as far up as the printed part allows. Using 6mm M2.5 screws - while definitely preventing bottoming out -  leaves dangerously low thread engagement.

Top of plastic part to the tip of the nozzle measures 61.6mm:
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

wile-e1, 2021-12-29:
The nominal design height for the top of the toolhead to the base of the nozzle is 61.5mm for all hotends in Stealthburner, so you're pretty damn close at only being 0.1mm longer.

The airflow is aimed downward at the nozzle, not flat across the nozzle, so I think this may be more of a perception that the nozzle is too low.  My BMO looks exactly the same as yours and it's working ok, but I will admit that when the silicone sock goes on the heatblock, it looks like the airflow to the nozzle may be getting blocked slightly.

I think this warrants a little more investigation.  For now, I have revised the toolhead to reduce the possibility of the supplied fasteners being too long.

AaronHerrick, 2021-12-31:
the problem is me.  I've been saying the stickout should be 1.7mm, I was wrong. it should be what it is:  ~2.4mm

raymondh2, 2022-01-07:
@Krieselwind Can you please try the latest parts and let us know if that fixes the issue for you?

Krieselwind, 2022-01-08:
I see no difference?!

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

AaronHerrick, 2022-01-08:
Please measure the distance as shown here: https://github.com/VoronDesign/Voron-Afterburner/issues/33#issuecomment-1002460699

Krieselwind, 2022-01-08:
61.7mm

AaronHerrick, 2022-01-08:
61.7 is fine.  The spec distance is 61.5mm.  different printers and plastics and measurements can account for that 0.2mm difference.

This mount is correct, the picture looks correct, and it should work correctly.  I made a mistake telling you that the stickout measurement should be 1.7mm.  the correct measurement for that should be around 2.4mm.  please refer to https://github.com/VoronDesign/Voron-Afterburner/issues/33#issuecomment-1003238959

It is better to measure from top of toolhead to nozzle (61.5mm)

I think we can close this issue now.

Krieselwind, 2022-01-08:
Ok, fine ☺️ thank you

Closed 2022-01-11.

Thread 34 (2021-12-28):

San Ace B52 does not fit

Scroeder, 2021-12-28:
I have a problem mounting the B52 fan. Had to dremel out the screw hole, but it seems that 2mm in diameter are missing.

[
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
](url)

wile-e1, 2021-12-29:
I have added a little clearance to the fan cutout for SB Main Body based on BadNoob's feedback on his San Ace fan  I do not have a B52 to test fitment though.  If you could print Beta2 and report back, that would be fantastic.  Thanks!

Scroeder, 2021-12-29:
Sure, where do I find the beta2 ?

wile-e1, 2021-12-29:
My PR isn't merged yet, but you can access it from here:

[https://github.com/VoronDesign/Voron-Afterburner/pull/38](url)

Scroeder, 2021-12-29:
Unfortunately it does not fit but definitely better. I removed a little material from the marked area. Now it fits so nice and flush.
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

raymondh2, 2022-01-08:
We have decided not to support this fan due to the B52 being a 52mm fan not fitting into the space constraints in the design. While it can be forced into place, we neither recommend nor condone this method of fitment.

Closed 2022-01-08.

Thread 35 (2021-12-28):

Unsupported brackets - Cura exclusive slicing tolerance

kamermans, 2021-12-28:
When printing the `main_body_beta1` in Cura with `Slicing Tolerance: Exclusive`, the supports for these overhangs (the green parts) are not printed at all, so the blue sections are unsupported spaghetti:

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

Here's the toolpath view in Cura:

`Slicing Tolerance: Exclusive`:
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

`Slicing Tolerance: Middle`:
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

This is the first issue I've encountered with `Slicing Tolerance: Exclusive` - I've printed an entire Voron 0.1 and a few Voron extruders with this enabled.  If `Middle` should be used, we might want to mention that in the docs somewhere.  I can put in a PR if that's the route you want to go (assuming the docs are on GitHub).

Settings:
Cura 4.12.0
Layer height: 0.20mm
Filter out tiny gaps: enabled (disabling didn't help)
Fill gaps between walls: everywhere

kamermans, 2021-12-28:
Here's the finished print.  There are 4 spots where this occurred (blue) and one that printed fine (yellow).

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

wile-e1, 2021-12-29:
I can understand how this is an issue with the settings you have shown.  Unfortunately with how thing the bridges are intended to be, you've found the scenario where they do not work.  In general, I think most people wouldn't be touching settings like that unless they had an understanding of the consequences.

The only way to really get around this is making the trim-away bridges thicker which could create other issues for most people who use "middle".  I can look into the issue a little.

I'd be interested to understand why you're using a different slicing tolerance.  Could you elaborate as to why?

wile-e1, 2021-12-29:
I also wanted to bring this to your attention that the slicing tolerance is listed in the "Experimental" features section of Cura..

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

I don't think there's much more here that I can do since this seems to be more of an issue with an experimental setting on Cura rather than a design concern.

kamermans, 2021-12-29:
Ah, good point, somehow it escaped me that this was experimental.  I was using it to print Voron parts on my Ender 5 which was not well-tuned and was overextruding on corners, making fitment of functional parts needlessly difficult.  It is a nice compromise in most cases since it doesn't lead to underextrusion that I might otherwise get if I reduced the flow.  Clearly this is a problem of tuning (acceleration, jerk, etc), and the fact that it's also experimental makes me totally content with closing this issue.  If you do need to tweak the bridges in the future, note that the top bridge printed perfectly since it ends up with two layers instead of one.

kamermans, 2022-01-07:
Just wanted to note that `slicing_tolerance = exclusive` is set as default in the official Voron 2 Cura slicer profile:
https://github.com/VoronDesign/Voron-2/tree/Voron2.4/slicer_profiles/cura/Voron_Cura

Closed 2021-12-29.

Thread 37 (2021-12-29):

SB clearence with Rapido strain relief

DaLeberkasPepi, 2021-12-29:
My Rapido Hotend came with an included strain relief. Which i know the early review units didnt have. But thats also was causing problems for me. With the included strain relief i cant get the Rapido to fit into the cable channels.
Printed Parts:
[Stealthburner_toolhead_rapido_rear_cw2_beta0, Stealthburner_toolhead_rapido_front_beta0]

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

My suggested solution would be to make a cutout at the side of the cable channel (like shown in the picture below)
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

raymondh2, 2021-12-29:
This is already being worked on

raymondh2, 2022-01-07:
@DaLeberkasPepi do the latest files fix the issue fo you?

DaLeberkasPepi, 2022-01-07:
I'm in the process of reprinting that piece. I'll post pictures of it in place but the new version looks good.

DaLeberkasPepi, 2022-01-08:
With the new version the rapido fits no matter what orientation it gets mounted in.

At the beginning i didnt know that i could rotate the heatsink when i removed the 3 screws (I did think it would have been a too tight press fit or something) so i could have made it work by rotating it maybe... sry.

But honestly i dont want anyone encourage to remove the 3 skrews to rotate the heater core only to tighten them wrong and bending the stainless steel heatbreak....

TLDR: Now it should work no matter how oriented your heater block gets mounted on rapido. Thanks wil.e and the Voron team for the great work!

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

Closed 2022-01-08.

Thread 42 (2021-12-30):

IGUS chain mount does not line up with cable hole

RealDeuce, 2021-12-30:
With the IGUS chain mount, the strain relief tab extends past the edge of the cover.  As a result, the zip-ties on the strain relief tab get pushed back toward the chain, and the wires all need to make a sharp 90° turn to get under the cover.

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

RealDeuce, 2021-12-30:
Using just one screw to move it back by the hole spacing helps somewhat (the cover is a lot easier to close), but it's not quite enough to allow the string relief to work properly.

raymondh2, 2022-01-07:
Can you please post some pictures that are a bit clearer about what's going on.

raymondh2, 2022-01-07:
I now understand the issue. Are there any reasons other than the wires making a sharp 90 degree turn? @RealDeuce

RealDeuce, 2022-01-07:
> Can you please post some pictures that are a bit clearer about what's going on.

If I had an extra chain end, I could mock it up, but as it is, I won't be able to take further pictures until the next time I take the CW2 apart... but I'll try describing the issue better.

With the IGUS chain ends, there's a strain relief tab that extends from the end of the chain end.  The purpose of this is to provide a place where you can use zip-ties or similar to bundle the wires and ensure they don't slide in and out of the chain when the chain flexes.

If you have a zip-tie at the end of the strain relief tab around the wires, that zip tie holds the wires in a position that is past the opening in the back of the cable cover, which means a wire exiting the end of the chain and properly attached to the tab needs to go backward toward the chain before it can enter the opening for the wires under the cable cover.

If the wires are properly attached to the tab, closing the cover will force the wires to make this bend and hopefully slide the zip-ties back along the tab.  With two spec zip-ties, this forces all the wires to make a tight 90° bend to enter the opening.  Three zip ties forces an even tighter bend.  If the mount holes on the arm are moved back so the tab ends approximately even with the edge of the stepper, the wires can do a nicely radiused bend into the opening under the cover and still be held properly by the tab.

On my setup, I initially put the end hole of the chain end into the second hole on the arm, moving it back about 7mm, which was a large improvement, but still not quite enough.  I ended up modifying the STL to move them back a few mm more, which provided for a nice bend in the wires.

raymondh2, 2022-01-07:
Closing as the design team does not see this as an issue.

RealDeuce, 2022-01-07:
> I now understand the issue. Are there any reasons other than the wires making a sharp 90 degree turn?

It's actually even more than 90° if the wires are properly held at the end of the tab, and even when using two zip-ties at the base of the tab, the bend is being made by closing the cover, which puts strain on the cover and hinge screw (and wires of course).

Since the wires are likely hidden from view while closing the cover, it may not be clear that the wires are the cause of the extra resistance and they may end up bent tighter than their then minimum bending radius, making a wire break more likely to be caused by opening and closing the cover.

Closed 2022-01-07.

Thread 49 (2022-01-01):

Blower Intake Not Centered

to-the-nth, 2022-01-01:
Latest Beta2 STL. Front view shows blower STL intake not centered to fan or body of STL.  Using a Delta BFB0524HH from Filastuder which appears to be authentic.  There are a lot of counterfeits out there.  Fan is not getting loaded quite as much as with the factory housing: 124mA @24V with original cover vs 114mA mounted in STL so the fan could be loaded more...

Back view shows fan well centered left to right. Hard to measure. Fan may need to be moved down relative to the top or intake hole moved upwards depending on design intent.

I would expect the intake hole size to be slightly greater than the inside impeller blade diameter?  I measure a 32.25 mm dia intake hole on the blower cover that was was removed while the STL is ~30mm.  There also is a ~3mm gap between the impeller blades and the intake hole while distance to the original fan cover is ~2mm.  The larger gap which could reduce efficiency? What is the thinking for how large the gap should be?

Looking forward to the release of the step files to allow local quick iterations.  Thanks for all the work!

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

raymondh2, 2022-01-01:
We are already aware and looking into it.

wile-e1, 2022-01-03:
The industry 'standards' for 5015s are about as loose as it comes with respect to placement of the impeller and dimensions of housings/mounting holes.

I was asked to offset the cutout for the fan inlet slightly, but this may not have been a good idea.  We're gathering data to try and figure out how best to address the issue.

to-the-nth, 2022-01-03:
I hear you.  I've modeled a blower for a DIY printer. The problem becomes way more complicated trying to create a single universal design optimized for all fans.  Two suggestions:

-Pick a few fans to support and create separate  STL's if necessary.  We do it for hot ends.  Hope the vendors don't change their tooling. Might make life easier in the long run.

-Design the CAD so it is modifiable.  I edited the AB-BN version 30 to adjust the spacing between the fan and the impeller.  Unwinding all the fillets and chamfers in the right order to get to a base editable core that I could start modifying was daunting.  In the end of course there were some simple fixes, but it took a lot of energy to get there.  Shout if there is anything I can help with.

evandepol, 2022-01-03:
Suggestion: while I like the idea of the integrated clamp, but given that there are already holding screws as part of the design in the present, it might be more pragmatic to have a number of separately-printed “blower fan shims” as individual and customizable parts.

These shims might be a suitable semi circular or crescent shape, that replaces the current clamp, be affixed with the screws, and could accommodate and be customized to the various 5015 fans.

It would essentially separate this part of the geometry from the stealthburner main body  geometry. Much easier for people to print and experiment with shims, than trying to provide and maintain multiple iterations of the SB main body.

AaronHerrick, 2022-01-08:
Please check with the Beta 3 stealthburner carrier. while we cannot completely eliminate offset we can reduce it.  I also have found that using the FHCS in the back, ou can slightly adjust most fans, but this adjustment is limited.

Eclypse3D, 2022-10-13:
I had the same problem with a Sunon Motor is off to the right of the housing by about 2.5mm but my Delta is spot on dead center.  I do not think it will affect much if at all however, but in my all white clear stealthburner its super obvious how off it is, as opposed to my copper one but there is not getting around it, if you try clearance anything in the cover you will reduce airflow or seal.

Headrush69, 2023-01-22:
> I had the same problem with a Sunon Motor is off to the right of the housing by about 2.5mm but my Delta is spot on dead center. I do not think it will affect much if at all however, but in my all white clear stealthburner its super obvious how off it is, as opposed to my copper one but there is not getting around it, if you try clearance anything in the cover you will reduce airflow or seal.

I had the same issue with a Sunon MF50152VX-1L02C-A99. So much for spending extra on a "better" fan. Swapped in a cheap Amazon GDSTime fan and much better alignment but still slightly off. Checked all dimension and printed Stealthburner is perfect.

With the Sunon fan, fitting is very tight. (Sanded down completely)
Would this alignment affect functionality or just be a cosmetic problem?

mWachu, 2023-03-13:
Same issue with Sunon fan and latest stealthburner release. This really sucks...
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

VoronManiac, 2023-03-13:
Part of the problem is there is no standard for blower fan dimensions.  Each manufacturer has their own footprint.  I think the Voron team has done a great job trying to find a common denominator. The design was been updated since my original post.  I am printing up the very latest STL's and will report back if we not in pretty good alignment.

Also stay away from under powered fans like the Sunon and stay with BB fans.  I highly recommend getting an authentic Delta BFB0524HH which will set you back under $20. Delta is rated at 160mA or 3.84W (easily measured)  where the Sunon is about 1/2 the power at 1.94W.  There are MANY fake versions of the Delta fan out there both from China and US sellers.  Confirm with the seller will stand behind the markings on the label.  I've had good luck with GDSTime GDB5015 which comes in at 100mA @24V for other applications and are available for $8 on eBay, but again, wouldn't recommended a lower powered GDSTime fan for this application.  The Delta is VERY loud running full tilt.  You can dial back the power in your slicer settings, but it is good to know you have the airflow for things like bridging.

mWachu, 2023-03-13:
>

Would you mind to show how this Delta fits? Looking for good 5015, currently got a 12v sunon but it has a huge offset from the center. Too much for my aesthetics :D

VoronManiac, 2023-03-14:
FYI I'm at 5000ft.  Just measured current to be 130mA @24V on BFB0524HH across four fans I got the fans from Filastruder.  The fan is pretty well centered side to side, but it does ride a touch high.

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

raymondh2, 2023-03-17:
This won't be fixed. Stealthburner was designed around the delta fan we recommend. It's not going to be perfectly centered on other fans

VoronManiac, 2023-03-17:
Form the photos I posed, I think it is looking good with the Delta fan.  Nothing to fix. The delta seems to be one of the more powerful fans out there for the money.  Great design choice.  Delta's are available from reputable 3d printer suppliers at least in the US and were also available from electronic supply houses like Digikey and Mouser at one point.  Just stay away from the cheap ebay counterfeits. Measure the current to know that you have a genuine Delta.

Closed 2022-01-21.

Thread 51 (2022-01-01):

Probe intersects with switchwire x carriage

xLAwildx, 2022-01-01:
PINDA style probe intersects with switchwire x carriage. There is a contour on the linear rail mount, but the opposite contour is missing from the x carraige.
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

stvptrsn, 2022-01-05:
Hi xLAwildx, the pinda probe has a really short, like 2.2mm, sense distance.  At the point the probe is interfering with the x carriage, like in your pictures, it is too far off the bed to trigger.  I just confirmed this on my Switchwire with the pinda probe installed
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
.

nife87, 2022-01-08:
I agree that its sense distance is short (I have a genuine SuperPINDA), but having just converted from AB v2.4r1 to SB beta 3 I disagree that the clearance is large enough. My probe is sitting 1.4mm above the nozzle, and there was not enough space, so I had to grind the corners a bit. See #57.

xLAwildx, 2022-01-08:
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
You can see here where I manually carved out part of each side of the x carriage so that I could move the probe high enough.
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
You can see in the second pic that this way I can move the probe mount up to level with the bottom of the carriage, which should be the max height.

wile-e1, 2022-01-21:
This issue should now be resolved with PRhttps://github.com/VoronDesign/Voron-Afterburner/pull/67

Closed 2022-01-21.

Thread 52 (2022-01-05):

Bottom heat sink fin on V6 is not properly cooled.

Dfdye, 2022-01-05:
The bottom heat sink fin on the E3D V6 heat sink is not enclosed within the area cooled by the tool-head fan.  The V6 heat sink measures 42.7 mm from end to end, and 39mm from the upper inside edge of the mounting groove to the bottom of the lowest cooling fin.  The SB mount for the V6 measures approximately 36 mm from the upper edge of the mounting groove to the bottom ridge of the cooling duct that encloses the heat sink (about 3mm short of what is needed, if my measurements are correct).  This leaves the lowest fin of the heat sink un-cooled, and in my case seems to have caused heat creep issues for me while printing PETG,  I don't have definitive evidence for this, but anecdotally the PETG will not experience heat creep when fitted with the ABBN.  As a point of comparison, the ABBN V6 mount appears to fully enclose the V6 heat sink within the area cooled by the tool head fan.

AaronHerrick, 2022-01-06:
this is certainly possible, what heat break are you using?  if it is one with a teflon liner, have you recently changed it the teflon liners oxidize over time, even at low temperatures.

Dfdye, 2022-01-07:
I tested with both a Ti heat break and a bi-metal Ti/Cu heat break.  Both were "all metal" and did not have tubing in the heating zone.  It may well be that I have something else going on (which is why I added the caveat in the initial post!), but so far it seems to be that the cooling from the SB is not working exactly right for my rig.

raymondh2, 2022-01-07:
We are looking into this

Dfdye, 2022-01-07:
Great!  Thanks for all of the work that you have already put into this.  You and the rest of the crew working on this are fantastic!

wile-e1, 2022-01-08:
A revised toolhead has been created and will come out with the next round of updates. Expect to see in soon.

Dfdye, 2022-01-08:
You guys are unbelievable!  Thanks so much for looking into it.

govido, 2022-01-15:
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

I can confirm that it is fixed with beta2 :)

Closed 2022-01-15.

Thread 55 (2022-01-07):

Not enough engagement on BMG gears. (Potential fix)

Wornie, 2022-01-07:
After updating from CW1 to CW2 I was getting huge skipping and extrusion issues.

I narrowed it down to the amount of clamping force on the filament between the two gears due to the guidler arms being too stubby.

I've modded up a quick fix that has completely fixed the issues on my end and I believe it might help solve potential edge cases similar to mine.

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

(Blue is the original guidler pieces, the grey is the shifted portion.)

By shifting the guidler's gear slightly more toward the main drive gear, the spring tensioner also has a larger adjustment range and allows for more tolerance in the bmg gears.

wile-e1, 2022-01-21:
This issue should be addressed with the changes made in PRhttps://github.com/VoronDesign/Voron-Afterburner/pull/67

Please try out the new parts and report back in a few days if the changes solve your issue.

Closed 2022-01-27.

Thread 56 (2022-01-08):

Issuing an Upgrade Warning

Durahl, 2022-01-08:
I think the Dev Team ( or the person curating the Manuals ) may want to add an Upgrade Warning/Notice that the new SB/CW2 combo will both change and _reduce_ the build volume in most if not all axes.

The MGN12 Carriage is ~4mm wider than the AB/CW one ( increasing the chance of a collision when attempting to reach `X0` on a 350 sized setup ), the Nozzle is being pushed like 3mm towards the front of the build volume ( necessitating the move of both the Z-Probe _and_ Build Plate ) and the increased height of the entire SB/CW2 assembly _reduces_ the Z-Build Volume height by 15-20mm.

AaronHerrick, 2022-01-08:
For X axis, are you using the same xy joints from the dual MGN-9 setup? the MGN12 requires new XY joints.  I don't know if that was explained in the manual.  Once you are using the correct xy joints you should have no issues in X or Y

For Y axis: The nozzle is in the exact same position as Afterburner.  the clearances in Y are in the exact same position.

For Z axis: here is a comparison of Afterburner to StealthBurner, this is approx 8mm.
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

wile-e1, 2022-01-08:
> I think the Dev Team ( or the person curating the Manuals ) may want to add an Upgrade Warning/Notice that the new SB/CW2 combo will both change and _reduce_ the build volume in most if not all axes.
>
> The MGN12 Carriage is ~4mm wider than the AB/CW one ( increasing the chance of a collision when attempting to reach `X0` on a 350 sized setup ), the Nozzle is being pushed like 3mm towards the front of the build volume ( necessitating the move of both the Z-Probe _and_ Build Plate ) and the increased height of the entire SB/CW2 assembly _reduces_ the Z-Build Volume height by 15-20mm.

Thanks for bringing this up.  The MGN12 carriage is 3.2mm wider than the standard MGN9 carriage, but the XY mounts were adjusted to accommodate this.  The cable chain contacting the top of the XY joint cap would and start to bind before the X carriage contacts the XY joint anyway.

As for the difference in Y that you mention, I'm not sure where you're getting this data.  The current CAD vs. the SB shows me that they are the same.  From the center of the X-rail, 91.7mm to the front face of the toolhead.

Current AB on MGN9 x2
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

Stealthburner on MGN12
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

As for the Z-height issue you mentioned, CW2 extends 2.7mm higher than the heights point on the existing Afterburner/CW1 design (which is the guidler latch).  However, the first point of contact (and the limiting part) is actually the Y-chain anchor that would contact the rear Z Idlers or the underside of the frame extrusion first.  So the different in height of the toolhead is inconsequential.

Durahl, 2022-01-12:
Sorry the late reply...

> As for the Z-height issue you mentioned, CW2 extends 2.7mm higher than the heights point on the existing Afterburner/CW1 design (which is the guidler latch). However, the first point of contact (and the limiting part) is actually the Y-chain anchor that would contact the rear Z Idlers or the underside of the frame extrusion first. So the different in height of the toolhead is inconsequential.

Yeaaa... Pretty sure the Bowden Tube, you're probably forgetting about, would like to disagree with _that_ assessment:
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
Any higher than `Z280` and I'm expecting an `M117` with a restraining order from its lawyer to pop up in my Console.
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
The difference may just be like 10mm but... Ya kno'?

So yea... 330mm
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
...have long since left the chat ( even with the AB/CW my previous `printer.cfg` had to have Z already capped to 300mm ) 🤔

Closed 2022-01-08.

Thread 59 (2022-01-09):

Two sharp corners broke layers while fast printing

adama119, 2022-01-09:
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

Since CW2 is beta version, I've just tried to use  Stealthburner on my My Voron2.4  with Clockwork 1 and Phaetus  dragon hotend. (Voron-Dragon HF Hotend)
But the LED sharp corner touch layer while printing randomly.   Sometimes layers are broken by the corner.
Can you fix this?  Thanks for all the work!

stealthburner_main_body_beta2.stl
stealthburner_toolhead_(dragon)-front-beta0.stl
stealthburner_toolhead_(dragon)-rear-cw1-beta0.stl

raymondh2, 2022-01-09:
The way you make it sound seems like your prints are warping into the ducts? Can you please elaborate on this issue.

AaronHerrick, 2022-01-09:
At all times, that corner is 2.3 mm higher than the nozzle unless there is something broken on your printer.

stantang986, 2022-01-10:
It happened to me as well when using Voron-Dragon HF Hotend only.
This hotend seems a lit bit shorter than normal one.

adama119, 2022-01-10:
> It happened to me as well when using Voron-Dragon HF Hotend only.
> This hotend seems a lit bit shorter than normal one.

Exactly the same,  My hotend is  Voron-Dragon HF Hotend

stantang986, 2022-01-10:
If you don't want to change stl file,
you can try to screw the toolhead front part first and then cover the main body part(the out red one), it may save you just a little bit distance.
Or, don't mind looking thing, jst cut it...

wile-e1, 2022-01-11:
I took a closer inspection to this issue and it does have some merit.  I have been using the Dragon mount and definitely noticed my toolhead is close to the build plate, but it still shouldn't be wiping your prints out unless they're warping or peeling up from the print surface.

With that said, the cutout that I was provided looks like it places the nozzle about 1.4mm higher than the target height, which absolutely does eat into the clearance. The Dragon mount has been adjust and will be updated on the repo soon. Please keep an eye out for Beta1 version of the toolhead files.

Thank you for bringing the issue to our attention.

vjeko2404, 2022-01-13:
I can confirm that with the dragon hotend and SB, the nozzle tip was only 0.7mm higher from the SB casing. My solution was to print 1mm distance washer for inbetween HE mount and the body.

Closed 2022-01-15.

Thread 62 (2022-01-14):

LED (RGB) Flashing

acosano, 2022-01-14:
My apologies if I posting int the wrong place but I have try FB and Discord with no success on anyone given response. I printed 2 sets of the Stealthburner. One is on my SW with a SKR1.4 and the other one I use on my new v2 build with Octopus Pro. The LED (RGB) working fine on the SW but not on the V2. the lights keep flashing with different colors and I can't control it. I'm using a harness from KB3D that came with the 3 additional wires for it. I'm using PIN0 <- Cero. I can measure the current off 4.99v. Any help would help

wile-e1, 2022-01-15:
> My apologies if I posting int the wrong place but I have try FB and Discord with no success on anyone given response. I printed 2 sets of the Stealthburner. One is on my SW with a SKR1.4 and the other one I use on my new v2 build with Octopus Pro. The LED (RGB) working fine on the SW but not on the V2. the lights keep flashing with different colors and I can't control it. I'm using a harness from KB3D that came with the 3 additional wires for it. I'm using PIN0 <- Cero. I can measure the current off 4.99v. Any help would help

Hi there, unfortunately this isn't really the right place to get help with this.  Issues are to keep document and keep track of design and operation issues with Stealthburner or Clockwork2.  The issue with your LEDs is an issue with your control board or possibly something to do with your wiring.  Some LEDs seem to be a little fussy about working on certain control boards.

The LED Discussion or the Electronics section of the Voron Discord are your best bet for getting help resolving this issue.

Closed 2022-01-15.

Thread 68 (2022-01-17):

Bearing block for SW unnecessary?

crashmaxx, 2022-01-17:
[a]_x_bearing_block_SW_beta0.stl is only used for SW, but the V2/Trident MGN12 carriage can mount to the same rail without this extra piece.

I suggest changing the SW carriage to mount directly to the rail, the same as V2/Trident. This would save an extra part, 4 screws, and 4 heat set inserts. I was able to redesign the original SW carriage in this way and have used it without issues.

Maybe I am missing an advantage of the extra block, but I suspect it exists simply because it was designed first. When Trident was designed, a better way to make the carriage was discovered.

wile-e1, 2022-01-21:
I think this Issue might be better raised in the Switchwire Repo since it is much more related to the design and function of switchwire than it is to Clockwork2.

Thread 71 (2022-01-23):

[SW-Beta1] Dragon ducts are too high after recent model update

DorjeDorf, 2022-01-23:
Hi,

I recently printed out the newest Dragon mounts (beta2 front and beta1 cw2).

Previously I had the beta0 for both.
I noticed that now, the ducts are very high - to the point, where the air is blowing on the sock and significantly impacts the PID profile - to the point of triggering heater fault when the fan kicks in. This was not the case with beta0. Now, they are as much of a problem as we've had the BMS mount before in ticket #26

When looking at the underneath of the mount - the bottom plate of the Dragon is sticking out of the mount - which was not the case with the previous version.

To be sure - are the socks not causing an issue here? If I take them out, just visually I can tell that air will not really impact the heatblock. But with the sock on - it seems as if some of it would be blocked the sock. I don't have a way of running a flow simulation, so I may be talking out of my ass here, but... I'm worried this is still an issue.

I'm attaching pictures below of before and after.

New ducts:
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

Old ducts:
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

DorjeDorf, 2022-01-23:
This is the TL version - bought a looong time ago ;)
Top of heatsink to nozzle: 46.7mm
Top of heatsink to heatblock - 41.35mm
Top of heatsink to heatblock with sock - 43mm

wile-e1, 2022-01-23:
I'm honestly not sure what is going on here.  The mount is designed to what all of the current specs are showing for dimensions (45.5mm).  The question is, why is your dragon longer than what the specs sheets say (and what other users have confirmed with their hotends)??  Your Dragon is longer than it should be. (by about 1.2mm)

Specs from Phaetus show the Dragon is supposed to be 45.5mm from top of heatsink to nozzle.  The Triangle Lab info i found also shows that.

The toolhead is design for 45.5mm.

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

Is it possible that you're using a non-standard V6 nozzle?

DorjeDorf, 2022-01-23:
The nozzle is from Trianglelab - a T V6. It looks different to a standard E V6, but lengthwise is the same (both are 12.5mm). Just to be sure - I exchanged it to a regular V6 type - problem remained, since the problem is visible also without the nozzle. The distance from the top of the heatbreak to the bottom of the heatblock is different than what you show.

The Dragon is very old - one of the first ones after they got released (it still has the V1 heatbreak). Maybe (like with the BMS) - something changed over time.

That said... Looking at that bottom image (with a blue dragon) - it seems there's more going wrong with my mount. The bottom of the dragon on your picture sits pretty much flush with the bottom of the mount - notice in my pictures - mine sticks out quite a bit.

Just to be sure, I'll reprint the mounts and check.

Can you just confirm one thing for me, please?
Does the sock not impact air flow? Looking at the bottom image - it seems as if there is no sock present there - not sure what was used for sims - and it's bugging me a lot ;)

zachdthompson, 2022-01-26:
Dragon v2 here, I just wanted to chime in and say I’m not having this issue. I built mine yesterday and it looks fine.

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

Im fairly certain this may be due to you having a v1 dragon. I tested both my standard flow and high flow dragons and they both fit.

DorjeDorf, 2022-01-26:
Actually, looking at your print @zachdthompson - I see the bottom of your Phaetus Dragon (judging by the heat block) protrudes underneath the bracket just as it does for me. This does not match what @wile-e1 posted in CAD.

I should finally be able to print my set today. Will update then.

alexeypetrenko, 2022-01-26:
Hi, I'd like to get some clarity regarding dragon mount as well.

Should the bottom of a heatsink be flush with the round cutout on the toolhead front and rear parts?

In my case it sticks out around two mm.
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
These are `beta1` parts. I'm printing front beta2 right now to test it. But it is mostly irrelevant, as this distance beta1 and beta2 parts is the same (24.5) mm

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

Also, it looks like the CAD cutout from [this post](https://github.com/VoronDesign/Voron-Afterburner/issues/71#issuecomment-1019569990) does not match STL parts and dragon heatsink dimensions.

Stl leaves 24.5 mm space for 26 mm heatsink. So, it should stick out 1.5 mm. Thickness of a heatsink is only 2mm in the thinnest part. So, it should stick out at least 3/4 of it's thickness. But on a cutout is sticks out just slightly.

Sorry if i'm being picky. Just trying to understand how it's supposed to be.

DorjeDorf, 2022-01-27:
I made another mount print - no changes for me, but I see others are also seeing the heatsink stick out from underneath the mount effect.

Caipitrooper, 2022-01-30:
Hi,
after trying the new Dragon beta2 mount, I found the same issue on mine.
So I imported the Dragon Front beta0 and beta2 into Fusion and compared them.
The measurements show, that the Hotend mount on the **toolhead went down 1.43mm** (beta0=14.57mm, beta2=16mm) while the overall dimensions of the tollhead stayed the same. The lower surrounding structure even went further up (beta0=40.57mm, beta2=40.50mm). This moves the Dragon 1.43mm down blocking more of the vent outlets and leaving more of Dragon's cooling plates outside the cooling window (1.5mm less of the cooling body).

Here are the images I took in Fusion360,
the Dragon Phaetus SB toolhead beta0:
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

and the Dragon Phaetus SB toolshead beta2:
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

AaronHerrick, 2022-02-03:
I think this may be from using longer nozzles.  Those of you with the issue can you post pics of your hotends with measurements with and without nozzle?

DorjeDorf, 2022-02-03:
To be clear - in my case, the nozzle is exactly the same length as expected regular V6. This data I have already provided above. There is a chance that I just have a different dragon from everyone - it would be helpful if someone with a V1 chipped in, since I think most people have a V2 (and that one has differences in heatbreak length and the radiator itself too - in V1 - the heatbreak sits flush against the heatbreak, while V2 has a small part pushed in, so the heat break goes a bit into the top plate).

That said, there seems to be a second potential issue where the radiator sticks out in the bottom - which does not match the CAD image.

AaronHerrick, 2022-02-03:
I have a trianglelab Dragon HF purchased in March 2020...this should be a v1.
It matches wile's and trianglelab's dimensions. 26mm heatsink, 45.5mm top of heatsink to nozzle

AaronHerrick, 2022-02-03:
I'm trying to reconcile all the data here, so one thing I did was try to pull some dimensions from your photo.

that looks OK to me in terms of overall length, did you make a measurement along the blue line here?
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

DorjeDorf, 2022-02-03:
Ah ok. If your heatbreak is like mine and it sits flush against the radiator (no hole in for the heatbreak to go into) - then yes, you have a V1. The main difference is in the thickness of the heatbreak - it goes along what Slice did with their heatbreaks, where v2 (as can be seen in the posting from alexeypetrenko) received an almost full length copper wrapping, whereas in v1 - it's only the radiator fins at the bottom).

The distance in my case for the blue line is actually 62.7.
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
AaronHerrick, 2022-02-17:
What are your PID onstants, and what wattage is your heater?  do you run that with or without a sock?

> Having the same issue here with my Phaetus Dragon HF. Air is blowing against the socket. If I run my blower at 100%. Temperature drops a lot and print fails. Can only run at 35/40% Fanspeed. I think the height is fine. It's more the angle of airflow but can't fix it without CAD files :D

AaronHerrick, 2022-02-17:
> Right, my thought was that could turn in to suction with the part fan running, providing additional cooling to the hotend. It's easy enough to test but really grasping at straws.

that can't really happen. not the way the duct is shaped.

The answer here is most likely more mundane.  When a problem occurs like this its common to look at the duct and think the answer is its blowing on the block.  After all, that's what is new to you, that would explain the data, so it seems reasonable.

But the real answer must explain ALL the data, including all of the other dragon tests.  there are hundreds of people using SB with Dragon (or its predecessor ABBN) with no issues.  If your dragon is the right height, and the duct works well for lots of others, there is another reason.  here are two I have seen:

1)PID_Kd term is too high/PID tuned with fan off.
Klipper's PID tune is very simple and can lead to bad answers.  if the Kd term is high (above 120 or so) that can lead to poor control

2)No sock/ heater underpowered
The heater might be up to the increased airflow

3)too large a smooth_time is used for the thermistor.  I think Klippers default is 1-2 seconds, you really only need .25 -.5 s of smoothing.

DorjeDorf, 2022-02-17:
It's difficult to have a constructive conversation here, where most of our questions are ignored.

Considering I started this thread, I'll say this.

1. My current status is I have bought a new dragon - V2. Now the lengths are correct. My guess is the problem with my V1 was the length of the heatbreak, but I won't be buying another one just to confirm this.
2. The heatsink sticks out from underneath the mount - multiple people have asked if this should be like that - I can't see an answer to these questions here, despite those being asked loads of times.
3. Now regarding the questions asked in the previous message, in my case - I am on a Duet and not on Klipper. My pid was done with the fan both on and off - duet calibrates both and has two curves for PID. I am using a sock - and actually I asked loads of times trying to understand where the issue is - if the sock should be on or not - no answer to that. Heater in my case was 50W before, now it's 60W - no change in behavior, but even a 40W should be more than enough. There is no smooth_time configurable on duet as it is in klipper (or I don't know of it).
4. None of these issues were present on AB-BN. It just worked for all of my hotends and worked really well.
5. Honestly, at this point - after having my questions ignored multiple times and seeing the thread was marked as invalid from the getgo - I won't be spending time here anymore. I appreciate the work that was put into the SB, but I don't appreciate the way our questions are being ignored. I mean how difficult is it to say - yes, it's weird the heatsink sticks out from the mount - we'll look into it; or no - this is the way it is going to work, thanks for noticing. Anything...

AaronHerrick, 2022-02-17:
DorjeDorf,
I'm sorry you feel that way.  For me, I am much more used to working on the discord server.
If you like I'd be happy to talk with you there either in a public discussion , ticket discussion (which only you and team members can see) or DM.  my user name is "Badnoob" and I designed the ducts and thermal performance of both SB and ABBN.

I apologize if if it seems I've been ignoring your questions. The bottom of the Dragon "heatsink" is really just a frame.  95% of the cooling is done by the small copper  finned section.  Its hard to say whether that frame should "stick out" or not, because that is a subjective term, and doesn't really impact the performance.  Your nozzle should be 61.5 mm below the toolhead top.  If that measurement is correct, and you are using the correct and latest sb beta files, you should be getting good performance.

Yes you should be using a Sock.

Without knowing the actual PID terms you have or having more data (such as cooldown curves with and without fan) I can't be much more help to you.

K4r98, 2022-02-20:
PID Tuning done with Fan on.
Socket on.
I bought a 50w Heater and it's able to hold the temperature :)

Airflow could be more downforced instead of blowing against the Socket but in my Case I am able to print with 100% Fan  :)

raymondh2, 2022-04-30:
Closing from inactivity

Closed 2022-04-30.

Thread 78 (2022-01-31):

No room for the collet on a Pheatus BMS

WanderW, 2022-01-31:
Hi, I'm trying to build a SB with a Pheatus BMS (6 fin version) I previously used this hotend in an ABBN-30 and it worked great there. In the SB it doesn't fit, because there is no room for the collet that holds the PTFE tube.
Because there is no room for the collar, the screwholes don't line up with the heatset inserts.

Stealthburner:
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

For reference the same mount from ABBN-30:
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

DorjeDorf, 2022-01-31:
Remove the collet - that's what I did. It won't be necessary considering the pressure coming from both halves of the mount that hold the tube in place.

timmit99, 2022-01-31:
Keeping the collet installed, while keeping the hotend stock, can make removal of the PTFE impossible without a full disassembly. Also, you would want to fit a collet clip in there as well\ to keep the tube from moving up and down during retract moves.

Removing the collet entirely and just having a spare one incase it gets damaged and you want to reinstall later is probably the easiest solution unless you see a NEED to have the PTFE captured inside the toolhead.

raymondh2, 2022-02-02:
Closing as we will not be making space for the collet.

raymondh2, 2022-02-02:
After discussion, removing the collet, while potentially damaging to the collet, allows for much easier replacement of the PTFE and servicing of the hotend. In this case we decided against adding the cutout therefore requiring the collet be removed.

Closed 2022-02-02.

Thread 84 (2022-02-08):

Incorrect screws in manual for front plate

jdknoll, 2022-02-08:
The last page of the manual specifies two m3 x 25 screws for the front plate on clockwork 2, but it should be m3 x 20mm or else the screws stick through pretty far.

wile-e1, 2022-02-08:
> The last page of the manual specifies two m3 x 25 screws for the front plate on clockwork 2, but it should be m3 x 20mm or else the screws stick through pretty far.

The page where the bolts are showed also has a big note next to it explaining this.

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

timmit99, 2022-02-08:
@jdknoll  the screws are designed to be a bit long to allow for them to be loosened for toolhead removal without coming out of the heat-sets entirely.
=)

jdknoll, 2022-02-09:
Thank you for the response! With the highlighted note, my assumption was that you would loosen them slightly as in just enough to loosen them, but not remove them - not that you would leave them in the insert as you swap out, so when I saw the screw go past to where the guidler is, I assumed that something was wrong in my assembly. That said, thank you again for the clarification.

Closed 2022-02-22.

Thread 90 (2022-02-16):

Rapido mount is oriented the wrong way

riley-williams, 2022-02-16:
The current rapido mounting orientation blocks the outlet on one side of the back piece (screwed in):

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

It looks like the opposite rotation was intended as that would hold it up against the front and out of the way of the back outlet. Unless rapidos come in both orientations...

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

DaLeberkasPepi, 2022-02-17:
If you carefully remove the 3 stabilizing screws, you can rotate the heat block. But be careful when tightening the 3 screws again to go carefully and bolt them evenly, so you don't bend the heatbreak.

riley-williams, 2022-02-17:
Is this something every rapido owner will be expected to do? If all rapidos come in 1 or 2 orientations, it seems like it would be much easier to just provide the parts that support the factory orientations.

riley-williams, 2022-02-17:
After playing with it for a little bit, I've changed my mind. Seems like a reasonably easy thing to ask everyone to do. I'll track down a set of official instructions from phaetus on safe reassembly and create a PR for a README that might help with future confusion for people that get their rapido in the 2 unsupported factory orientations

wile-e1, 2022-02-17:
Is your Rapido a Phaetus or from some other vendor?

riley-williams, 2022-02-17:
Mine is a TL Rapido

nathanielhudson, 2022-02-18:
If you want another datapoint, I also have a TL Rapido and had the same factory orientation as riley. Disassembling and reassembling to correct this wasn’t too bad though.

wile-e1, 2022-02-25:
Since we've added the note for now, thanks to @riley-williams , I'm going to consider this issue closed for the time being.

Closed 2022-02-25.

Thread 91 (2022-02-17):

Dragon hotend is loose even when screws are fully tightened

mathiasm74, 2022-02-17:
The four M2.5 screws that came with my HF Dragon have 12 mm thread. Fully screwed into the hotend, 7 mm thread is still visible, but the holes in the Afterburner are only about 5.5 mm deep, meaning the hotend can move up and down almost 2 mm even when the screws are fully tightened.

raymondh2, 2022-02-17:
Try using some M2.5x8

dmpmassive, 2022-02-17:
The wholesale Dragon's that come in kits like the Formbot seem to ship with M2.5x12mm and the Retail Box has M2.5x8mm.

mathiasm74, 2022-02-18:
Yeah, found my regular flow Dragon I bought earlier, and it came with 8 mm screws. Have modified the STL in Tinkercad now, but a lot of people must have the same problem.

geterdonek, 2022-02-18:
This is noted in the sourcing guide.

hmouridsen, 2022-02-18:
My Phaetus Dragon came with shorter screws meant to be used with V0 - they fit absolutely perfect

wile-e1, 2022-02-19:
While it may be noted in the V0 sourcing guide, it could certainly be more visible elsewhere.  I just don't know what the looks like yet.  But using 8mm long bolts is the solution to this "issue".  We cannot control what hardware ships with vendors kits.  All phaetus hotends that I've received generally come with a few different lengths of bolts.

We will figure out the best place to document what's needed for the builders.

Closed 2022-02-19.

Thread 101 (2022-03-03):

SB Rapido Toolhead Mount (Front) Beta 4

flyespresso, 2022-03-03:
On the bleed air ports, I they're not fully extruded on the Rapido toolhead. Printed and can verify nothing passes through, looked at SS slice (with PIF settings) and confirmed, then took look at STL and yeah, they never intersect. Confirmed as an issue with wile.e & timbot99 on Discord. Adding here as requested :)

Video on Discord: https://cdn.discordapp.com/attachments/923325119454126090/949021443730079804/Screen_Recording_2022-03-03_at_11.01.08_AM.mov

Part Link: https://github.com/VoronDesign/Voron-Afterburner/blob/sb-beta/STLs/Stealthburner/Toolheads/phaetus_rapido/stealthburner_toolhead_(rapido)-front-beta4.stl

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

wile-e1, 2022-03-05:
This issue has been corrected in PR #103

Thanks for bringing it out our attention.

Closed 2022-03-12.

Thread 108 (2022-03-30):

Cable Cover Foul on V1.8

Makhaira, 2022-03-30:
I've just assembled the CW2 plus SB on a V1.8 MGN12 build. When facing the printer from the front, approximately 6mm of travel is lost from the X axis due to the cable cover fouling on the XY joint.

The point of the foul is around the attachment screw. The cover itself fouls, however removing it still results in a foul as the securing screw for the cover then impacts the XY joint.

Easy fix: A 6mm block is added to the underside of the X gantry which allows the X endstop switch to be triggered. The printer therefore is fully working, but 6mm of travel is lost.

Complicated fix: The cable cover and securing screw position requires moving to avoid this foul.

raymondh2, 2022-04-01:
Voron 1.8 is considered a legacy printer now. As such development might not account for it

Makhaira, 2022-04-01:
Absolutely get that, recognise that Trident is the current offering in that family now. Given the high number of 1.8s in the wild though would it not be worth considering it?

With the joys of written communication don't take this as me being argumentative, just challenging if the user base is large enough to warrant consideration, even with it being legacy.

raymondh2, 2022-04-01:
The number of V1.8 printers built is tiny compared to the other printers we are supporting.

wile-e1, 2022-04-02:
> Absolutely get that, recognise that Trident is the current offering in that family now. Given the high number of 1.8s in the wild though would it not be worth considering it?
>
> With the joys of written communication don't take this as me being argumentative, just challenging if the user base is large enough to warrant consideration, even with it being legacy.

This was already discussed in the Stealthburner channel after you brought it up and a definitive answer was already given.

1.8 is no longer a current model which means it may or may not be supported.  There were a lot of 2.1 and 2.2's out in the wild as well, but those models were not considered either because 2.4 is the current version.

I will not be making any changes to the design, but once we hit release.....CAD will also be released and someone will most likely come out with a modification for 1.8.

Closed 2022-04-02.

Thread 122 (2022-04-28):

[a]_stealthburner_main_body_beta7.stl hole when slicing.

mlee12382, 2022-04-28:
When I sliced [a]_stealthburner_main_body_beta7.stl using SuperSlicer 2.4.58.2 and using multi color painting I found a hole when inspecting the tool paths, it appears in the upper right mounting hole and only seems to occur when I have it set to the secondary color for contrast. Initially I thought it was a result of a modification I had made but after some testing I was able to reproduce it on the unmodified stl also.
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

wile-e1, 2022-04-29:
> When I sliced [a]_stealthburner_main_body_beta7.stl using SuperSlicer 2.4.58.2 and using multi color painting I found a hole when inspecting the tool paths, it appears in the upper right mounting hole and only seems to occur when I have it set to the secondary color for contrast. Initially I thought it was a result of a modification I had made but after some testing I was able to reproduce it on the unmodified stl also.

I am definitely not seeing this same issue SS 2.3.57 (which in my experience is the last stable version there has been of SS in months).  The screenshot here shows all of the standard Voron settings with the addition of "overlapping perimeters=off" and "thin walls=off".   So if there was a hole....  this would absolutely show it.

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

So I'm going to close up this issue, because it is clearly a slicer issue.

mlee12382, 2022-04-29:
It only shows up when I "paint" that area using multimaterial painting, which is not available in 2.3.57, I will test it on PrusaSlicer to see if it shows up there also and update.

wile-e1, 2022-04-29:
> It only shows up when I "paint" that area using multimaterial painting, which is not available in 2.3.57, I will test it on PrusaSlicer to see if it shows up there also and update.

The design is not optimized with multi-material printing in mind.  If the part works when you print it with 1 color and it doesn't when you try to do weird slicer stuff to it, that isn't an issue with the STL.

mlee12382, 2022-04-29:
Ok, just thought I would bring it to your attention in case it was something you wanted to address, does the same thing in PrusaSlicer btw.
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
Thanks for your time :)

mlee12382, 2022-04-29:
Any chance you might have an idea of how I can fix it on my end?

wile-e1, 2022-04-29:
I'm guessing it has to do with the fact that there aren't 2 full walls thickness there.  I can probably rework that area to make sure it's atleast 2 walls thick.  Otherwise, I don't have any experience with MM, so I'm not really much help.

mlee12382, 2022-04-29:
Hmm ok, maybe I will try painting the inside of that area the same color and see if it fills the hole if that's the issue. Thanks for your time and suggestion  :)

mlee12382, 2022-04-29:
Well that kinda fixed it but there was 1 tiny line that I couldn't get to fill in, so I will just avoid painting around that hole, thanks again for your help :) Quick question on the dual bowden parts for AB, they should fit sb still correct?

Closed 2022-04-29.

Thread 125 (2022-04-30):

How to use adxl_washer

XEL-Maker, 2022-04-30:
I printed out the parts needed for adxl 345 mounting.
There was also a washer_x2, so I printed it, but I couldn't imagine how it would be assembled.
Someone asked for an image on a closed issue related to this, but there has been no comment since.

XEL-Maker, 2022-04-30:
I tried a few more times after writing the issue.
And I assembled it as shown in the picture.
Do you fix the adxl with m2 self tapping?
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

kaibsora, 2022-05-03:
you fix it with the supplied washers that are in the same folder, with the m2 self tapping screws. the screws go through the washer, and then self thread into the mount. you cant just use the screws, as the holes are too big, the washers fix that issue.

BeardedTinker, 2022-05-03:
Also, the washers have cutout on one of the surfaces - that part goes over those capacitors near the hole to protect them from both contact and damage if thightening too much.
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

XEL-Maker, 2022-05-03:
Thank you for the information.
I'll have to install it as needed.

Closed 2022-05-03.

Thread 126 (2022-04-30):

cable door problem

XEL-Maker, 2022-04-30:
When applying toolhead pcb, interference occurred in cable door, so processing was performed.
Could you add the version where the area was removed?
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

I used this pcb.
https://github.com/hartk1213/MISC/tree/main/PCBs/Stealthburner_Toolhead_PCB

res:
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

For the smooth mounting of the substrate and CW2,
two 3.3mm thick spacer was used.
Interference still occurs even when the spacer is not used.

raymondh2, 2022-04-30:
This is not the repo to report this issue. As the PCB is not an official part of CW2

Closed 2022-04-30.

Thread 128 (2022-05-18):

Clockwork2 MR85ZZ bearing housings in the motor plate and main housings are different diameters, 8.2mm and 8.1mm

AxlePivot, 2022-05-18:
When printing both parts with identical settings I found the bearing fitted easily in the main body but would not fit in the motor plate housing. Measuring the .stl gives 8.1mm for motor_plate-beta10.stl and 8.2mm in main_body-beta11.stl.
8.2mm was preferable for a gentler push fit without warming the ABS.

iwm911, 2022-07-24:
I didn't checked the stl size but I can say that the bearing just doesn't fit in the motor plate.
I can push it in but then it clicks when the gear is turning

raymondh2, 2022-07-26:
Closing as beta has ended

Closed 2022-07-26.

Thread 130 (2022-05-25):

Filament Engagement Issue

Durahl, 2022-05-25:
Greetings...

I was having a busy week with my `Beta0` parts causing me to looe grip which I assume must have had its root in one of the Accent parts keeping tension on the Drive Wheels. The System has an **ERCF** as part of it which is kinda adding _a lot_ of friction along the way the Filament has to go through, but I never had any issues until now.

So, with that I decided to make the jump to the current `Beta7/10/11` Parts since I had to reprint them anyway and have noticed it being practically worse than with the deformed parts. After lot of back and forth I noticed a bunch of issues:

- The Filament Path appears to be unusually large in diameter? I was able to fit a 2.1mm Drill bit into it with ease whereas with the old Afterburner I recall the necessity of boring it to size - Is this supposed to be the case?
- Unlike with the Beta0 Parts where the Filament was grinded equally flat on both sides the Beta7-11 ones would cause only the Passive Gear side ground flat whereas the Active Gear Side would remain pristine.
While feeding a Filament through the open System ( no Motor Plate ) I noticed the Filament making practically no contact with the Active Gear - I can also practically not see the Gear while viewing it from the top through the Filament Path.
Grinding is most definitely not the goal but, in my ( Pamphlet sized ) Book having only one side ground flat is kinda worse, no?
- Without the Active Gear but the Passive Gear Installed I noticed a somewhat similar trend where I was able to pass the Filament through the path with it just barely making any more contact than with the Active Gear.
Bringing the Passive Gear closer is impossible due to the top edge of the Lever resting on a Lip of the Main Body ( above the Ramp ) and the Shuttle also being too long when fully seated.
The Filament **_does_** get properly gripped when both Gears engage it but apparently not enough under certain situations with all the ERCF Friction going on along ( influx of humidity in recent days? Dunno... ), the Active Gear not being situated in the Filament Path and the Passive Gear ( or rather the Lever it is mounted to ) bottoming out before getting a secure hold onto the Filament.
( My biggest Suspect for the Friction Problem also being the Entry / Exit holes of the ERCP Buffer Zone as they're not perpendicular to the Wheel the Filament is getting spooled onto - [Especially not the Exit one feeding to the ERCF](https://i.imgur.com/et7Aa7A.png). )

While I'm at it some questions that have also popped up ever since making the change to the Stealthburner:
1. The 10T Stepper Motor Gear is only making Contact with about ⅔ of the BMG Plastic Gear ( back side ) leaving about ⅓ ( front side ) untouched despite the Axle making contact with the Stepper Housing ( visible grinding marks ). Are we supposed to grind the Axle down in such a case to both improve the engagement between the Gears and to prevent the Axle from making contact with the Stepper Housing? At the same time I notice the Axle already not being proud in a properly seated front Bearing kinda indicating that this one too would have to be shifted further inwards for the axle to still be making a reasonable amount of contact with the inside of the Bearing? 🤔
2. May I suggest the addition of a third cooling channel from the Hotend Cooling Fan towards the inside of the CW2 like how it was done for the bottom of the Part Cooling Shroud? I cannot shake the idea that it may aid in preventing like the Levers and Bearing Retainers from deforming while under constant tension while getting heat soaked from the Hotend and Stepper Motor?
3. Is there a chance for an early access to the CAD Solids? I've since done okay modifying the STLs via Modifiers in the Slicer to suite my needs but realigning the Bearings to fix the Active Gear Filament Engagement issue is beyond tedious doing it like that 😑

Cheers 😁

xinqi9083, 2022-06-29:
Same problem,  I had to replace my CW2 with Orbiter 2.0

raymondh2, 2022-07-26:
Closing as beta has ended

Closed 2022-07-26.

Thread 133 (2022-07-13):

[suggestion] Stealthburner add missing STL for X Carriage

pdion891, 2022-07-13:
Hi,
Would it make sense to add following stl files to the X Carriage since these are required to complete the installation of straps and bottom 9mm rail ?

* https://github.com/VoronDesign/Voron-2/blob/V2.4r1/STLs/VORON2.4/Gantry/X_Axis/X_Carriage/%5Ba%5D_belt_clamp_x2.stl
* https://github.com/VoronDesign/Voron-2/blob/V2.4r1/STLs/VORON2.4/Gantry/X_Axis/X_Carriage/x_carriage_pivot_block.stl

Regards,

raymondh2, 2022-07-26:
Fixed in release

Closed 2022-07-26.

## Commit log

2019-12-23 BETA1 Release of the VORON Afterburner Upgrade
    [_belt_clamp_x2.stl, _blower_housing_front.stl, _connector_cover.stl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]
2020-08-01 Afterburner release version (#4)
    [[a]_belt_clamp_x2.stl, [a]_blower_housing_front.stl, [a]_connector_cover_V1.8.stl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]
2021-05-20 Updated Afterburner Clockwork. Additional clearance around the BMG gears, new latch setup and wire cover. (#10)
    [[a]_belt_clamp_x2.stl, [a]_connector_cover_18.stl, [a]_connector_cover_24SW.stl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]
2021-08-31 Removed unnecessary Gantry folder.
    [[a]_blower_housing_front.stl, [a]_connector_cover_18.stl, [a]_connector_cover_24SW.stl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]
2021-08-31 Updated STL names to reflect application and print color. Updated [a]_blower_housing_front/rear to latest versions.
    [[a]_blower_housing_front.stl, [a]_connector_cover.stl, [a]_latch_shuttle.stl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]
2021-08-31 Added extruder_motor_plate.stl from Trident which add's MGN12 compatiblity to Afterburner Clockwork.
    [extruder_motor_plate.stl]
2021-08-31 Added toolheads for the Phaetus Dragonfly BMS and BMO hotends.
    [printhead_front_dragonfly_bmo.stl, printhead_rear_dragonfly_bmo.stl, printhead_rear_dragonfly_bms.stl]
2021-08-31 Updated CAD files to reflect changes in ab_pr_210828
2022-02-14 PR AB 220213 (#85)
    * Updated single and dual inlet bowden files. Updated CAD assemblies with latest changes.
    * Corrected print orientation for updated files.
    [bowden_dual_front_a.stl, bowden_dual_front_b.stl, bowden_module_front.stl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]
2022-02-21 Added toolhead files for the E3D Revo Micro. (#98)
    * Added toolhead files for the E3D Revo Micro.
    * Forgot to set print orientation. Fixed.
    * Corrected extra zip tie mounts on the Revo Micro Toolhead.
    * Updated CAD assembly with the E3D Revo Micro toolhead.
    [printhead_rear_e3d_revo_micro.stl]
2022-04-20 Added Revo Voron and Rapido toolheads. (#117)
    * Added Revo Voron and Rapido toolheads. Updated parts with cross-bridge countersunk hole method. Updated CAD.
    * Corrected missing fillet in fan duct. Resolves issue #115.
    * Changed all 4.8mm heatset insert holes to 4.7mm. Resolves issue #15.
    * Updated CAD with PR changes.
    [[a]_blower_housing_front.stl, blower_housing_rear.stl, bowden_rear.stl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]
2022-04-26 Added Revo Voron hotend model to the CAD assembly. (#121)
